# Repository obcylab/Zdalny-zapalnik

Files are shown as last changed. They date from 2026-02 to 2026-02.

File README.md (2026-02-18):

# Zdalny system zapłonu do rakiety
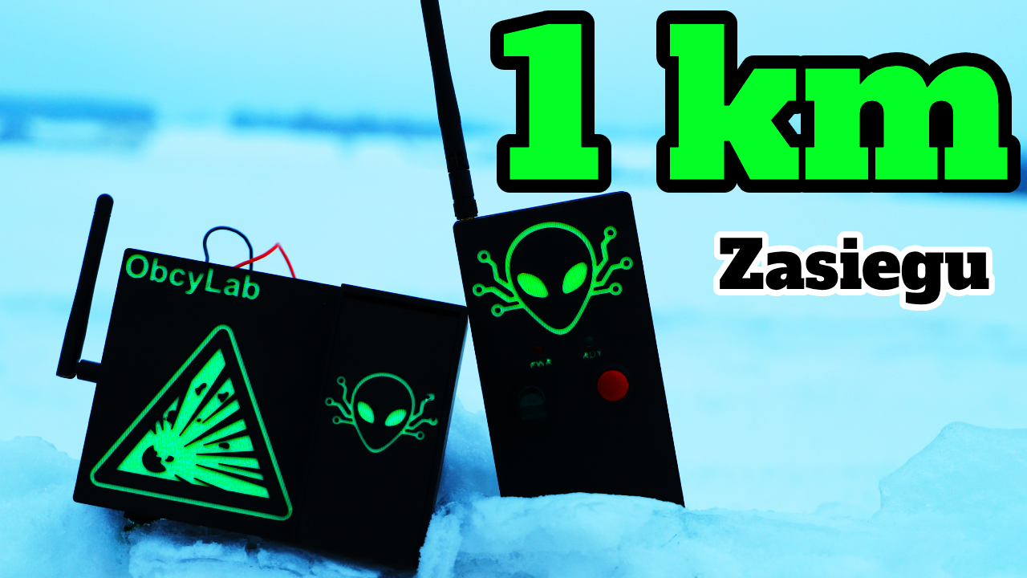
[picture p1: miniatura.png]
Miniatura

Jest to zdalny system zapłonu do rakiet modelarskich opartych na silnikach na paliwo stałe.  
Składa się z dwóch elementów: pilota i zapalnika. To urządzenie da Ci możliwość zachowania bezpiecznego dystansu  
przy każdym starcie Twojej rakiety. Jest to stosunkowo prosta, ale i niezawodna konstrukcja w odróżnieniu  
od tanich gotowych modułów.  

W repozytorium znajdziesz pliki z programem oraz pliki z **modelem 3D** do wydruku.

## Raspberry PICO Firmware
W zależności jakie masz Raspberry, taki wybierz firmware, jeśli:
- Raspberry PICO WH - RPI_PICO_W-20251209-v1.27.0.uf2
- Raspberry PICO H - RPI_PICO-20251209-v1.27.0.uf2

## Narzędzia

Lista potrzebnych narzędzi:
- Pistolet na gorący klej
- Lutownica + cyna [jeśli jesteś kreatywny, dasz radę bez]
- Drukarka 3D [Służy do zrobienia obudów, można ją zastąpić natynkowymi puszkami elektrycznymi większych rozmiarów]

## Pilot

Jest to urządzenie przenośne, dzięki któremu wysyłasz sygnał zapłonu do zapalnika.

### Lista elementów:
- Moduł nRF24L01+ [Taki z anteną]
- Raspberry Pico H lub W [H EAN: 5056561803180, W EAN: 5056561800196]
- Koszyk na baterie [EAN: 903351248860]
- Włącznik dźwigniowy [EAN: 5904422311650]
- Przycisk [EAN: 5904422304119]
- Dioda LED zielona
- Dioda LED czerwona
- 2x Rezystor 10k ohm [EAN: 5904422329280] - w sumie to byle był jakiś rezystor
- Kondensator elektrolityczny 4,7 uF [EAN: 5903351248303]
- Kable montażowe żeńskie [EAN: 5903351243032]

### Schemat połączeń
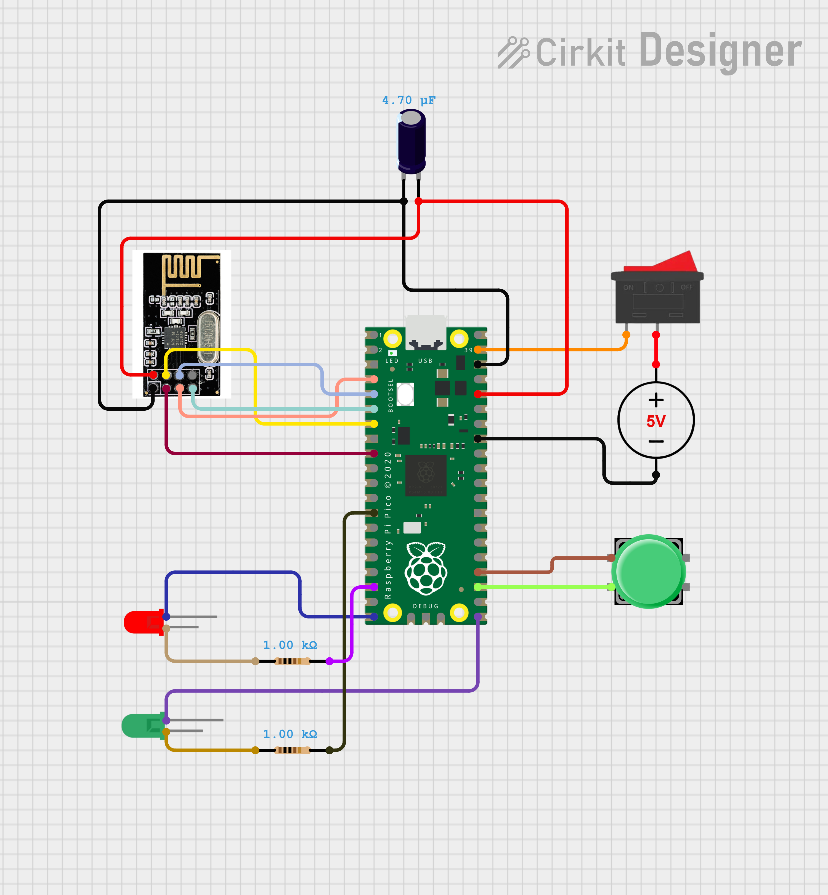
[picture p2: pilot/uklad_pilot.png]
Schemat Pilot


### Kod
W kodzie znajdują się zmienne, które można zmienić pod siebie

~~~python
###### Uzupełnij tę sakcje ######
# Zmien ten klucz tak aby zawierał 16 znaków (tak dokładnie 16 znaków)
# klucz musi byc taki sam dla obu urzadzen
klucz = b"rakieta123456789"
# Adresy powinny byc takie same na obu urzadzeniach
# Jesli nie plnujesz brac udzialu w zlach "rakieciarzy" to zmien tylko jeden bajt czyli:
# masz "\xaa" zamien na "\x67" w obu adresach ("\x" to jest staly element tego nie mozesz ruszac
adresy = (b"\x55\xf0\xf0\xf0\xaa", b"\x44\xf0\xf0\xf0\xaa")
#################################
~~~

Z adresami radzę za bardzo nie szaleć, bo potrafi przestać działać. Zalecam zmieniać zgodnie z tym, co powyżej.

## Zapalnik

### Lista elementów
- Moduł nRF24L01+ [Taki z anteną]
- Raspberry Pico H lub W [H EAN: 5056561803180, W EAN: 5056561800196]
- Przekaźnik [EAN: 5903351241229]
- Akumulator AGM 12V 1,2 Ah [EAN: 5902367802523]
- Włącznik dźwigniowy [EAN: 5904422311650]
- Dioda LED zielona lub inna wedle uznania
- Dioda LED czerwona
- 2x Rezystor 10k ohm [EAN: 5904422329280] - w sumie to byle był jakiś rezystor
- Kondensator elektrolityczny 4,7 uF [EAN: 5903351248303]
- Kable montażowe żeńskie [EAN: 5903351243032]
- Kable AWG22 - lub po prostu grubsze kable od tych montażowych w celu podpięcia akumulatora i  
wyprowadzenia zasilania na zapłonnik
- x2 Konektory wsuwane - można zastąpić krokodylkami lub innymi (podłączenie akumulatora)
- x2 Złącza krokodylki
- x2 Złącze WAGO (5 miejsc)
- x1 Złącze WAGO (3 miejsca)

### Schemat połączenia
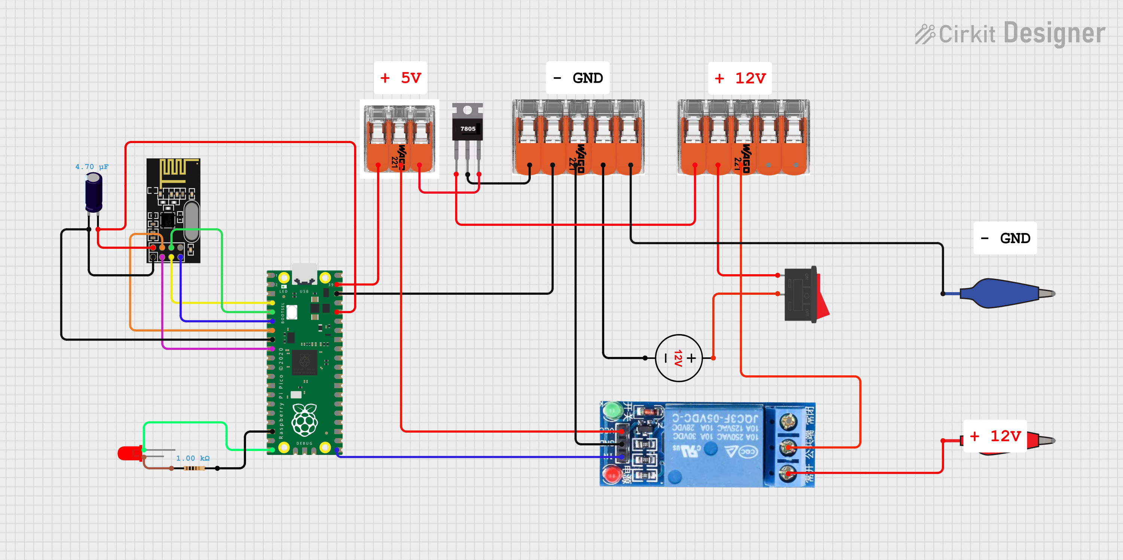
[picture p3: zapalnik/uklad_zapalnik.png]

### Kod

W kodzie znajdują się zmienne, które można zmienić pod siebie.

~~~python
###### Uzupełnij tę sakcje ######
# Zmien ten klucz tak aby zawierał 16 znaków (tak dokładnie 16 znaków)
# klucz musi byc taki sam dla obu urzadzen
klucz = b"rakieta123456789"

# Adresy powinny byc takie same na obu urzadzeniach
# Jesli nie plnujesz brac udzialu w zlach "rakieciarzy" to zmien tylko jeden bajt czyli:
# Zmien "\xaa" na "\x67" w obu adresach ("\x" to jest staly element tego adresu nie mozesz zmieniać)
adresy = (b"\x55\xf0\xf0\xf0\xaa", b"\x44\xf0\xf0\xf0\xaa")

# Podaj ile ma czasu (sekundy) ma zostać podane napięcie na zapalnik!
czas_nagrzewania: float = 3
#################################
~~~

Z adresami radzę za bardzo nie szaleć, bo potrafi przestać działać. Zalecam zmieniać zgodnie z tym, co powyżej.

## Używanie

Należy uruchomić pilot oraz zapalnik włącznikiem, a następnie:
1. Na pilocie znajduje się dioda oznaczona RDY. Ona sygnalizuje, czy pilot połączony jest z zapalnikiem.  
Dioda ta może palić się ciągle lub szybko mrugać, co oznacza stabilne połączenie,  
jednak gdy mrugania będą dłuższe niż 1 sekunda, oznacza to spadek jakości połączenia,  
ale nie oznacza to jego utraty. Dopiero gdy RDY nie będzie się palić, to znak braku połączenia.
2. Po wciśnięciu przycisku dioda RDY powinna zgasnąć na czas ustawiony na zapalniku (domyślnie 3 sec).  
Jest to oznaka, że zapalnik wykonuje polecenie zapłonu.
3. Na zapalniku powinna zapalić się jedna dioda w momencie, gdy jest on włączony, jednak gdy otrzyma on sygnał  
o uruchomieniu zapalnika, zapali się druga na czas podania napięcia na zapłonnik (domyślnie 3 sec),  
następnie gaśnie, co oznacza tryb gotowości.

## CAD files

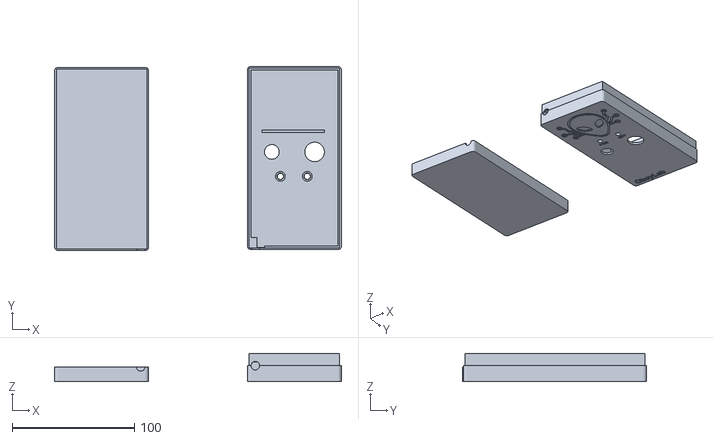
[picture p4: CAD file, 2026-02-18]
pilot/pilot.stl
234.8 x 150.8 x 23.0

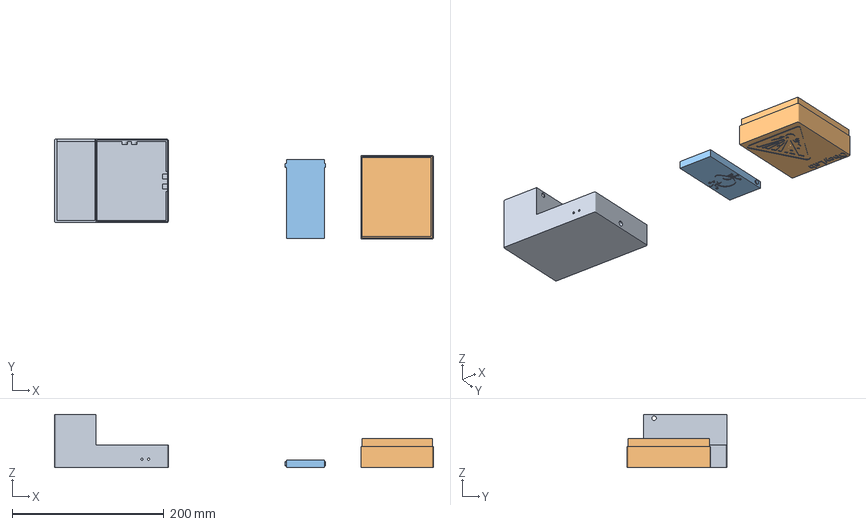
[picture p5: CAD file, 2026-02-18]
zapalnik/zapalnik.3mf
499.1 x 131.6 x 70.0 mm
zapalnik.stl_1
zapalnik.stl_2
zapalnik.stl_3

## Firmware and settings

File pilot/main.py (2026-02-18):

###### Uzupełnij tę sakcje ######
# Zmien ten klucz tak aby zawierał 16 znaków (tak dokładnie 16 znaków)
# klucz musi byc taki sam dla obu urzadzen
klucz = b"rakieta123456789"
# Adresy powinny byc takie same na obu urzadzeniach
# Jesli nie plnujesz brac udzialu w zlach "rakieciarzy" to zmien tylko jeden bajt czyli:
# masz "\xaa" zamien na "\x67" w obu adresach ("\x" to jest staly element tego nie mozesz ruszac
adresy = (b"\x55\xf0\xf0\xf0\xaa", b"\x44\xf0\xf0\xf0\xaa")
#################################


import utime
from machine import Pin, SPI
from nrf24l01 import NRF24L01
from micropython import const
import ucryptolib

_RX_POLL_DELAY = const(15)
_RESPONDER_SEND_DELAY = const(10)

power_led = Pin(15, Pin.OUT).high()
paired_led = Pin(16, Pin.OUT)
paired_led.low()
ignition_button = Pin(18, Pin.IN, Pin.PULL_UP)

cipher = ucryptolib.aes(klucz, 1)

CMD_RDY = cipher.encrypt(b"RDY-COMMAND-HASH")
CMD_IGN = cipher.encrypt(b"IGN-COMMAND-HASH")
CMD_DONE = cipher.encrypt(b"DON-COMMAND-HASH")

spi = SPI(0, sck=Pin(2), mosi=Pin(3), miso=Pin(4))
csn = Pin(5, Pin.OUT, value=1)
ce  = Pin(6, Pin.OUT, value=0)
nrf = NRF24L01(spi, csn, ce, payload_size=16)

nrf.open_tx_pipe(adresy[0])
nrf.open_rx_pipe(1, adresy[1])
nrf.start_listening()

num_failures = 0
rdy = False
msg = 0

while True:
    nrf.stop_listening()
    if rdy and ignition_button.value() == 0:
        payload = CMD_IGN
    else:
        payload = CMD_RDY

    try:
        nrf.send(payload)
    except OSError:
        print("Cant send (no ACK)")
        nrf.flush_tx()

    nrf.start_listening()
    utime.sleep_ms(5)
    start_time = utime.ticks_ms()
    timeout = False
    while not nrf.any() and not timeout:
        if utime.ticks_diff(utime.ticks_ms(), start_time) > 100:
            timeout = True

    if timeout:
        print("failed, response timed out")
        msg = 0
        paired_led.low()
        num_failures += 1
    else:
        msg = bytes(nrf.recv())
        cipher = ucryptolib.aes(klucz, 1)
        print("Recieved: ", cipher.decrypt(msg))
        if msg == CMD_RDY:
            rdy = True

            msg = 0
            paired_led.high()

    utime.sleep_ms(15)
